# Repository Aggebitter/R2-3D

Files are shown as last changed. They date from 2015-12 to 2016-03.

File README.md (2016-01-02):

# R2-3D

My home brewed coreXY 3d printer
The name "R2-3D" is a tribute to R2-D2 and his creator George Lucas who made me just love things that moves by software, 
electronics and pure mechanics.
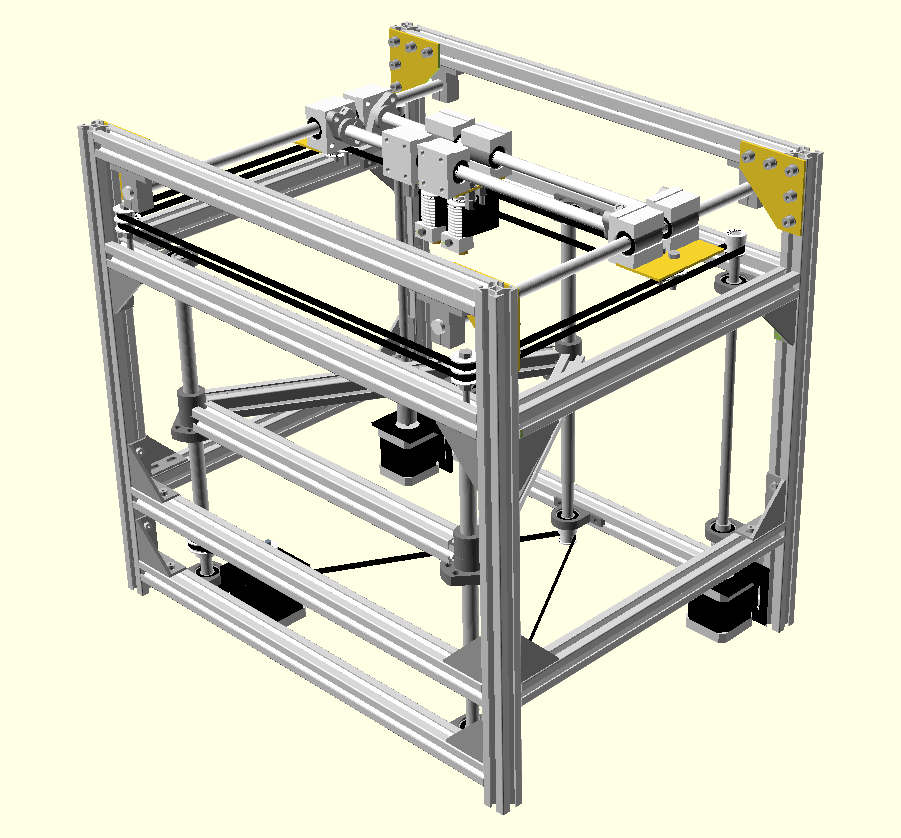
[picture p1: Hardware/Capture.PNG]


History:
A few years ago I put together a 3d printer kit from Welleman. 
It was their K8200 and I call it "put together" because it was like building Lego or Mecchano for us born back in the 70s.
I had a lot of fun with it and the complete build took about 24 hours from opening the box to the first print out.

But after some use I was not so impressed by the prints and a whole summer vacation full of modifications
did not satisfy me. There where too many issues with the design and I soon reached the end of the road.
The mechanics was not an big issue... it was the basic design.

After reading a lot of forum threads,and I meen a lot...! I started to notice a pattern with the same problems occuring in
most of the common and open designs of 3d-printers.

The roundup is as follows:

Z-Axis 
Printbed not as flat as needed for a solid gripping first layer

X and Y differs from the Z plane at diffrent locations due to slack or gravity bend on the axis

Heatbed does not deliver the high temperatures needed for printing ABS and other tough filaments

An asymetric drive of the axis contributes to both a diffrence in the Z-plane and a non perfect angle on the moves

ABS warps due to the fact that it shrinks when getting cold. 

This is all about mechanics!

You can try to fix some in software like autoprobing, primeing the first layer, slack compensate 
and so on, but all is still just quick fixes and if you just change filament you have to start all over and 
re-tweek your firmware

CoreXY:

There are some flavours of this type of coordinate system. But as I see it is only one basic design that is the "real" stuff
ref: http://corexy.com/theory.html

The CoreXY has benifits from other more common coordinate systems. It pulls and holds the movement on the X- and Y-axis in 
four points all the time. It sits on the top of the printer and that makes it possible to have a fixed Z-plane in the X- and 
Y-axis and only a linear move in the verical axis. This is a better aproach from the desings where the printbed moves in more 
than one plane. It gives us higher control of the critical Z-plane and fewer factors that will interfer with the need for high 
precision. 

The design with X- and Y- in the top just invites for a heatchamber. But then we shuold try to minimize the amount of motors and 
electronics in the heated volym. 

This Git is my part on delivering back stuff to the comunity of open source and open designs 
But it is still "in the making" My prototype printer works and it's time to start releasing it

My first dry run https://youtu.be/AdaIRemX2_0

// Agge

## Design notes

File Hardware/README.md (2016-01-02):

The folder OpenSCAD contens files for the R2-3D printer. The files are the base set for the upcomming drawings. 
The set is not complete yet

R2-3D is built on common hardware that you can by from Ebay and your local harware store.
The prototype is made with minimum machining and the design will include both 3D-printable-, CNC-mashining- and handtooling- sketches

The prototype is mecanical solid with 10mm linear bearings and all parts in alumium or steel. 

Micro controller: Arduino Mega

Shield RAMPS 1.4 (reprap.org)

Stepper drivers DRV8825 (more amps and voltage)

Wantai NEMA17 steppers rated 2.5A

Aluminium profiles 20x20mm from http://www.motedis.com or for Swedish users http://www.motedis.se

corner mounts, T-slot nuts and bults from http://www.motedis.com or for Swedish users http://www.motedis.se

Nuts, bolts and brackets mostly from Bauhaus hardware store.

BOM will follow soon

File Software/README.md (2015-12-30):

My Config for the very well written firmware Repteier
ref: http://www.repetier.com/

And my arduino sketch for the supporting Arduino UNO/Nano 
Under  development, not a running code !!!!

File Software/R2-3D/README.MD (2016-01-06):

## R2-3D

This is the very much under developmnet of my supporting co processor for the R2-3D printer.

The concept is to not fidle around in the main printer firmware just sniff the trafic on the serial interface and do some 
other nice taskt like controling RGB leds and making sounds (Well, R2-D2 feels like a good feedback voice for R2-3D9) 
Depending on the final R2-3D it might do the heat chamber controll. 

### main features that are under development is as follows:

Display printer head's and printer bed temperatures (It does sniff att 250000 Kbit and display it on my 7-segment)

RGB leds (noting done yet, just got the hardware)

Sound (noting done yet, just got the hardware, but found some nice files, aka ringtones in MP3 format)
Please Lukas art, Don't kill me for telling ;-)

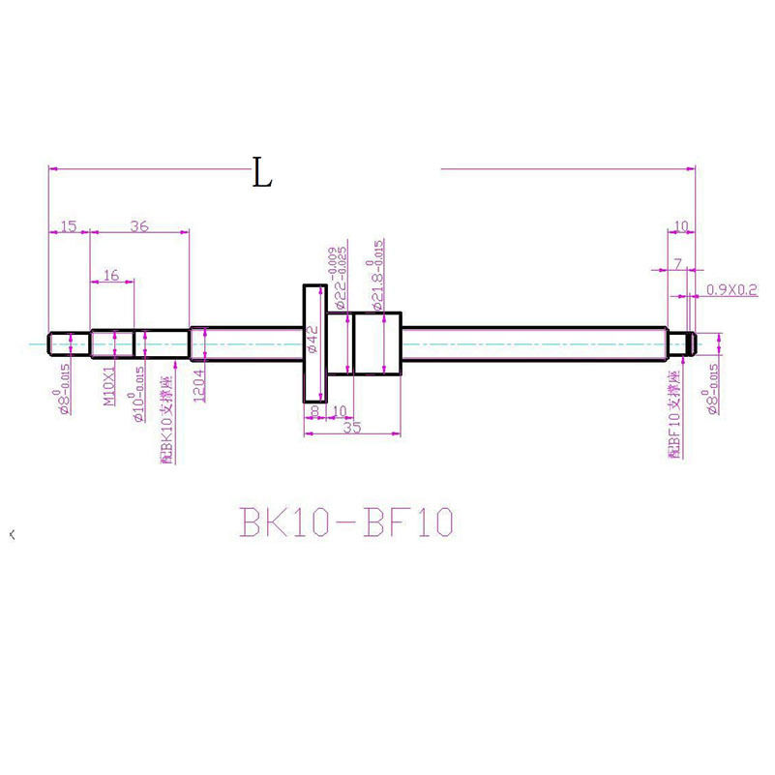
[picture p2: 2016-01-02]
ReferenceDoc/Ballscrew1204_BKBF10.jpg

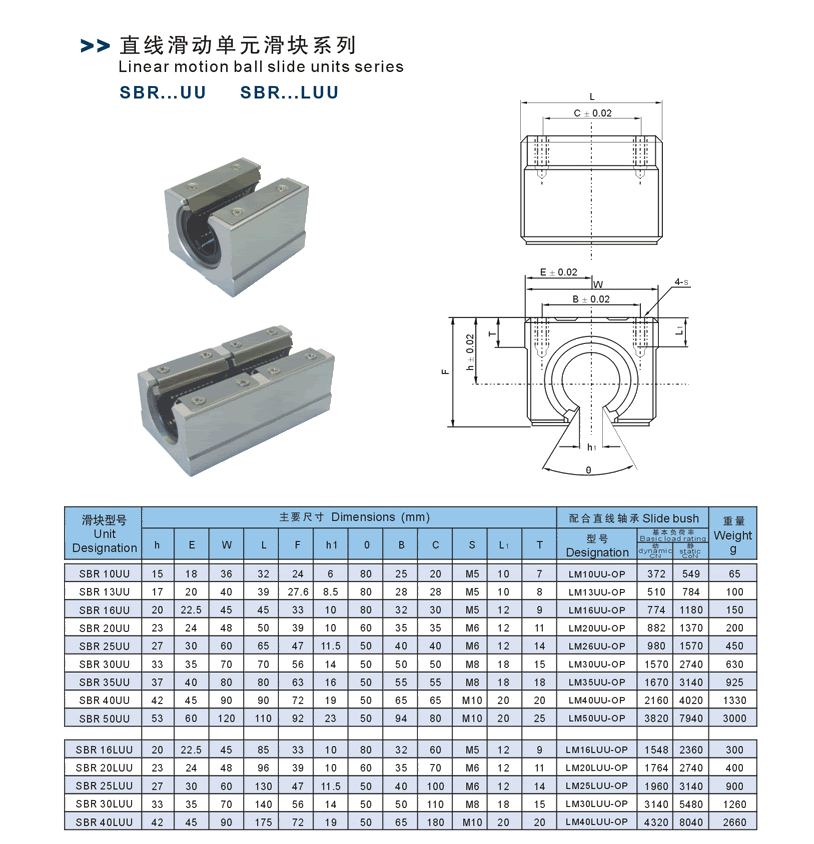
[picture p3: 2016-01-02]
ReferenceDoc/SBRxxUU.gif

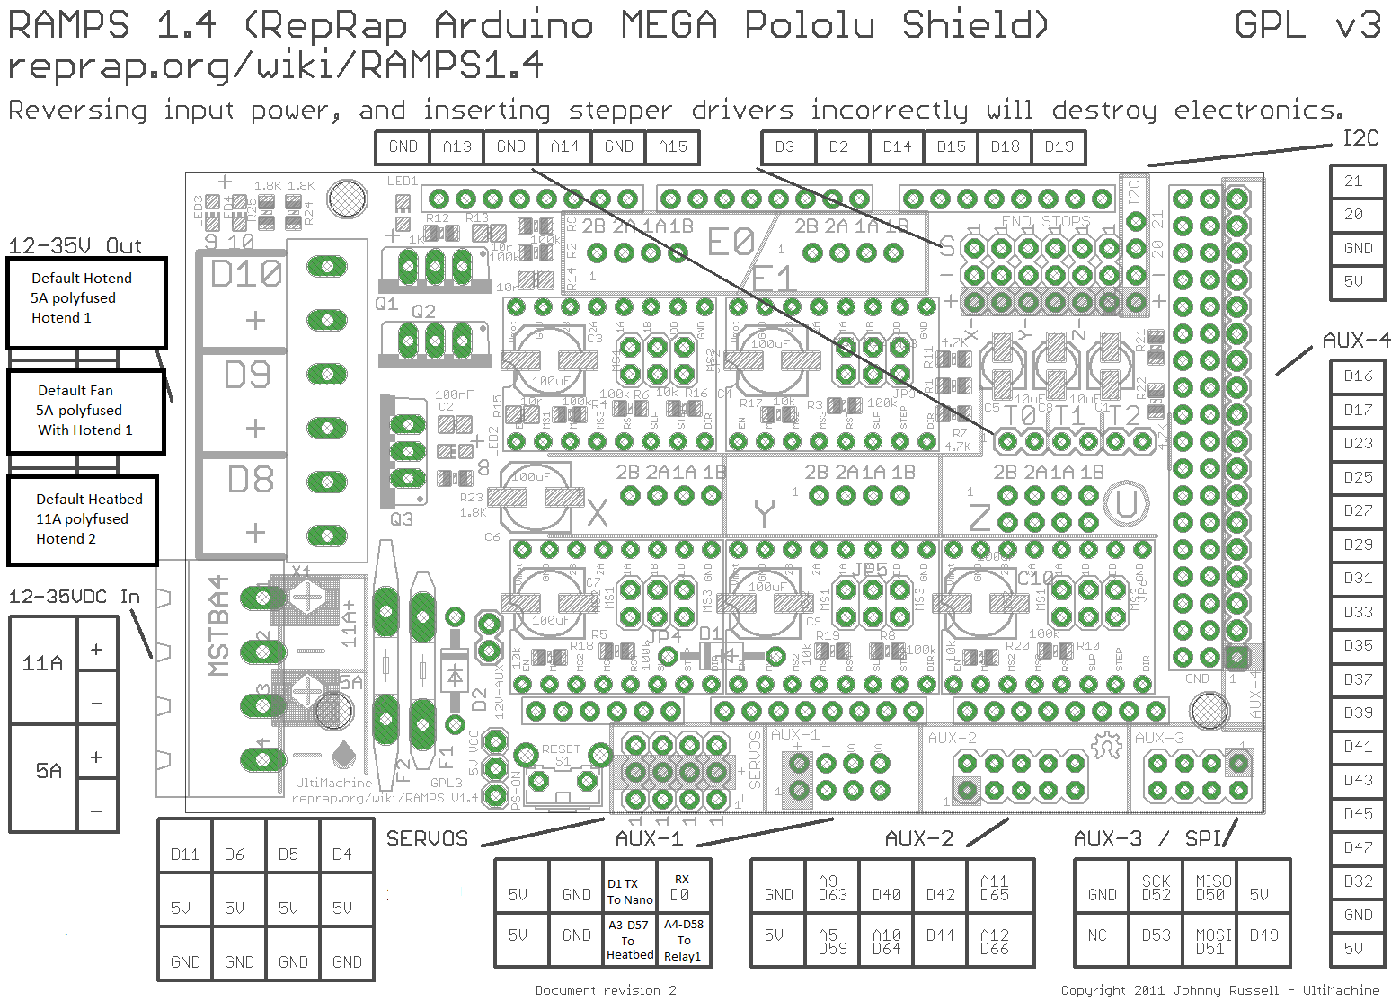
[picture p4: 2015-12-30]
ReferenceDoc/Ramps1.4_R2-3Dv1.0.png

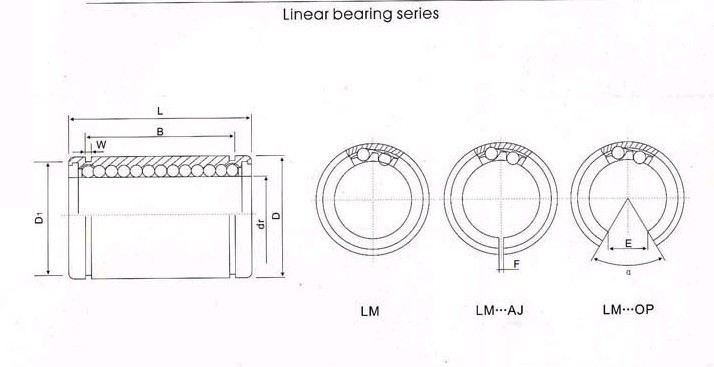
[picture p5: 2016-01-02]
ReferenceDoc/LMxxUU.jpg

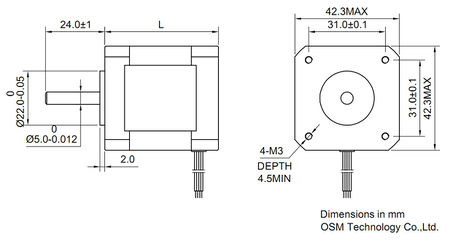
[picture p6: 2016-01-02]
ReferenceDoc/nema_17_stepper_motor.jpg

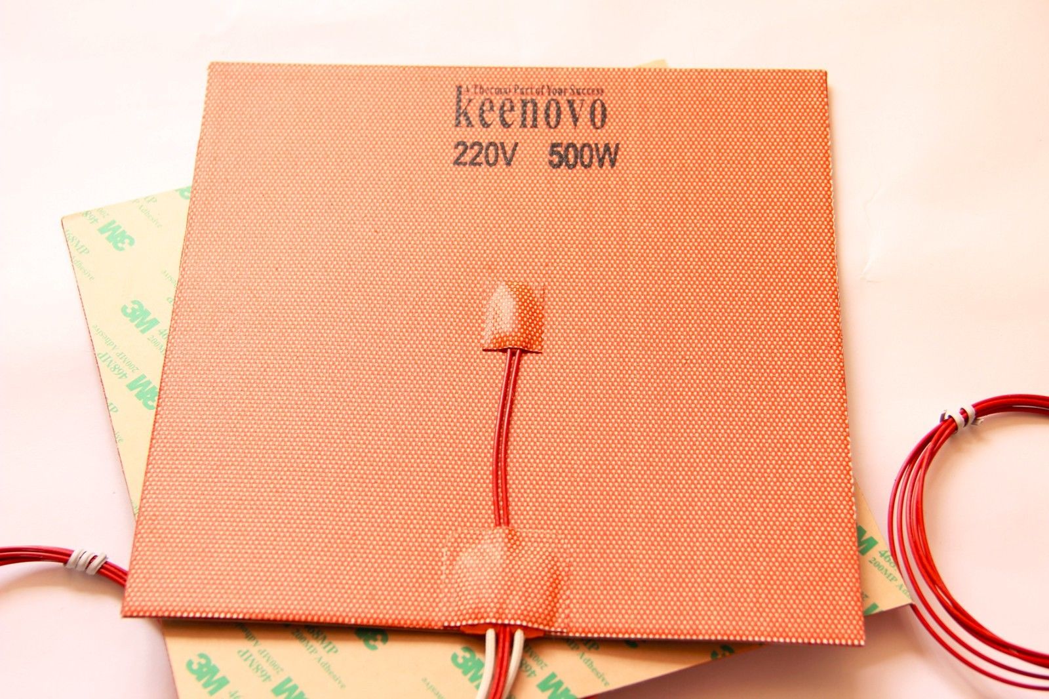
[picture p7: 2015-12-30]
ReferenceDoc/Keenovo.jpg

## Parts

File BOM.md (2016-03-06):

###------------------------  ALUMINIUM PROFILES and mounts -----------------------------

From www.motedis.com (www.motedis.se, for Swedish orders)
 
Profile 20x20 I-Typ slot 5 

Frame
410mm 4pcs (for 300mm ballscrews, if longer ballskrews are used, add the difference in length )
400mm	7pcs
300mm	4pcs

Heatbed mount
290mm	3 pcs

Top
!!!!Not donne yet!!!!!

Bracket 20x40 I-Type slot 5 www.motedis.com (90 degres mount)

18 pcs

T-Nut with spring ball, without guidance I-Type slot 5

200 (two bags) the exact amount not finish yet

Node plate nickel plated aluminum 60x60 (New home made CAD files soon on GitHub)

4 pcs

Aluminium Rod 8mm
300mm 2pcs (for 300mm ballscrews, if longer ballskrews are used, add the difference in length)

###---------------------------------  MECHANICS ----------------------------------------

Ballskrew end maschined 
SFU1204 300mm 3pcs

40 Teeth GT2 Timing Pulley Bore 10mm (drive and gearing down 2:1 Z-axis)
1pcs

20T 5mm GT2 Timing Drive Pulley
1pcs (Z-axis)

20T 8mm GT2 Timing Drive Pulley
5pcs (for CoreXY shafts x2 and ballscrews x3)

Stepper MotorShaft 5x8 mm Flexible Coupling
2 pcs

GT2 timing belt
5m (2.5m for the printer and one spare)

GT2 timing belt loop 
976mm 2pcs (one for spare, Z-axis}

GT2 timing belt loop (this one is to short and i had to machine out some material from the stepper bracket!!)
158mm 2pcs (one for spare, Z-axis}

Axle bearing, self centering 8mm bore
KP08 10pcs

Linear mechanics:
Liner Rail Linear Shaft 10mm diameter
300mm 2pcs
330mm 2pcs

Linear Rod Rail Shaft Support
SHF10 10mm 4pcs

Linear Rail Shaft Guide Support
SK10 10mm 4pcs

Linear Open Bearing 
SBR10UU 10mm 8pcs (Open blocks for matching hole dimensions and max travel, replace the bearings with LM10UU)

Linear Ball Bearing Bush Bushing
LM10UU 10mm 8pcs (for mounting in SBR10UU blocks, see not above)

Alloy Steel Mounting Bracket For 42mm NEMA17 Stepper Motor With Screws 5x5x5cm
5 pcs

Stepper MotorShaft 5x8 mm Flexible Coupling
2 pcs

SG15 5x17x8mm U Groove Sealed Line Track Guide Pulley Rail Ball Bearing (for filament mounting)
6 pcs

#Bolts

Size Lenght amount DIN-standard Standard (Use)

M4 10 10 DIN 7984 (Steel Mounting Bracket For stepper motor [only 8 pcs if only using one extruder)

M4 14 20 DIN 7984 Bore Ball Bearing (KP08)

M4 16 6 DIN 7984 Z-plane

M5 8 93 DIN 7984 (Bracket 20x40 I-Type slot 5 and Optical Endstop Switch)

M5 10 4 DIN 7984 (For Optical Endstop Switch on SBR10UU)

M5 12 8 DIN 7984 Open Linear Bearing, SHF10

M5 14 8 DIN 7984 Linear Rail Shaft Guide (SK10)

M5 16 3 DIN 7984 (For Ball Bearing for Filament)

M5 25 2 x

M5 30 1 y

M5 35 1 Extruderplate

M6 16 8 xy, Open Linear Bearing (SBR10UU)

#T-nut
M4 36 T-slot spring nut, for I-typ T-slot 5mm

M5 116 T-slot spring nut, for I-typ T-slot 5mm

#Spring washer

M4 36

M5 116

###-----------------------------  ELECTRONICS common -----------------------------------

Arduino Mega 2560 
RAMPS v1.4

Nema17 Wantaimotor Stepper  42BYGHW811 4800g.cm 2.5A (For fast print you need amp and voltage)
5pcs

KEENOVO Silicone Heater Pad 20X20cm 500W220V 
HeatedBed 1pcs

5pin 22AWG cable
10m

APTINEX Dual Channel Triac Module MOC3061 BT139 600V 16A (for a 230V 500W AC heatbed on digital pin57)

100K ohm NTC B4267 ATC Semitic 104GT-2 Thermistor
Thermistor 3pcs (You almost never nows what thermistor is used in chines clones, replace them ;-) )

Bowden J-head Hotend E3D V6 extruder
2pcs

MK8 Extruder dedicated Aluminum Frame Block
2pcs

Rocker Switch with red light KCD4-201N 4 pin on/off 16A/250V 
2pcs (Mains and enable/disable heatbed]

Optical Endstop Switch 
RepRap Mendel Prusa modell 3pcs

###--------------------------  ELECTRONICS R2-3D specific  -----------------------------

Supporting processor:
Arduino Nano
Expansion-Board-Terminal-Adapter-DIY-Kits-for-Arduino-NANO-IO-Shield-V1-0-S

5V MAX7219 8-Digit Red LED Display Module 7 Segment (for nice view of current temeratures)
2 pcs 

##Addons ;-)

U-disk audio player TF SD card voice module MP3 Sound WTV020-SD-16P
LM386 Audio Amplifier Module Board 5V-12V (sound is great;)
Loudspeaker 8Ω 0.25W 8ohm Small Trumpet 29mm

Printer head lights:

Adafruit NeoPixel Ring 24 x WS2812 5050 RGB LED (not sure if I am going to use it yet)

WS2801 2801 Dream Color 5050 RGB LED strip
5 meters

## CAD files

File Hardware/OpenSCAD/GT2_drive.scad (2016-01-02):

/*
lib for
20 toothed GT2 belt drive 5mm shaft h =16
20 toothed GT2 belt drive 5mm shaft h =16
40 toothed GT2 belt drive 10mm shaft h =17
*/
module GT2_20_5() { // 20 tothed GT2 belt drive 5mm shaft
$fn=50;
color( "White", 1 ) {
difference (){
    union (){
    cylinder (d = 16, h = 7.5, center = false);
    translate ([0,0,7.5])
    cylinder (d = 12.5, h = 7.5, center = false);
    translate ([0,0,15])
    cylinder (d = 16, h = 1, center = false);
    }
       translate ([0,0,-1])
        cylinder (d = 5, h = 18, center = false); 
}
}
}


module GT2_20_8() { // 20 tothed GT2 belt drive 8mm shaft
$fn=50;
color( "White", 1 ) {
difference (){
    union (){
    cylinder (d = 16, h = 7.5, center = false);
    translate ([0,0,7.5])
    cylinder (d = 12.5, h = 7.5, center = false);
    translate ([0,0,15])
    cylinder (d = 16, h = 1, center = false);
    }
       translate ([0,0,-1])
        cylinder (d = 8, h = 18, center = false); 
}
}

}
module GT2_40_10(){ // 40 tothed GT2 belt drive 10mm shaft
$fn=50;
color( "White", 1 ) {
difference (){
    union (){
    cylinder (d = 18, h = 7, center = false);
    translate ([0,0,7])
    cylinder (d = 29, h = 1, center = false);
    translate ([0,0,8])
    cylinder (d = 25, h = 7, center = false);
    translate ([0,0,15])
    cylinder (d = 29, h = 1, center = false);
    }
       translate ([0,0,-1])
        cylinder (d = 10, h = 18, center = false); 
}
}
}

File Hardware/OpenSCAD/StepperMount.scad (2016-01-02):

/*
Stepper steel mount
NEMA 17 Stepper
*/
$fn=50;
module StepperMount (){     //Stepper steel mount 
color( "Black", 1 ) {
union (){
difference (){
   
     cube ([50,52,53.5]) ; 
    
     // difference starts here  
   translate ([-1,3,3]) 
     cube ([52,52,53.5]) ; 
    hull() {
        translate ([8,3,13]) rotate ([90,0,0])
        cylinder(d=4.2,h=10, center = true);
            translate ([8,3,42]) rotate ([90,0,0])
        cylinder(d=4.2,h=10, center = true);
       }
    hull() {
        translate ([42,3,13]) rotate ([90,0,0])
        cylinder(d=4.2,h=10, center = true);
        translate ([42,3,42]) rotate ([90,0,0])
        cylinder(d=4.2,h=10, center = true);
    }
        translate ([25,31,-1])
        cylinder(d=22,h=10, center = true);
        translate ([10,46,-1])
        cylinder(d=3.5,h=10, center = true);
        translate ([10,15,-1])
        cylinder(d=3.5,h=10, center = true);
        translate ([41,15,-1])
        cylinder(d=3.5,h=10, center = true);
        translate ([41,46,-1])
        cylinder(d=3.5,h=10, center = true);

}
difference (){
        translate ([0,3,3])
        cube ([3,20,15]) ; 
        translate ([4,3,18]) rotate ([127,0,180])
        cube ([5,20,30]) ; 
}
difference (){
        translate ([47,3,3])
        cube ([3,20,15]) ; 
        translate ([51,3,18]) rotate ([127,0,180])
        cube ([5,20,30]) ; 
}
}
}
}
module NEMA17 (){           //NEMA 17 Stepper
translate ([25,31,3.01]) rotate ([0,180,0]) {
$fn=50;
difference (){
union (){
translate ([0,0,-23]){
color( "Black", 1 ) 
difference (){
cube([42,42,30], center = true) ;
      union (){
        difference (){
            rotate ([0,0,45])
            cube([60,60,50], center = true) ;
            rotate ([0,0,45])
            cube([50,50,52], center = true) ;
}}  
    
}

color( "Gainsboro", 1 ) 
difference (){
    union (){
        translate ([0,0,19])
        color( "Gainsboro", 1 ) 
        cube([42,42,8], center = true) ;
        translate ([0,0,-19.5])
        cube([42,42,9], center = true) ;
}
    union (){
        difference (){
            rotate ([0,0,45])
            cube([60,60,50], center = true) ;
            rotate ([0,0,45])
            cube([53.5,53.5,52], center = true) ;
}}}
}

    color( "Gainsboro", 1 ) 
    cylinder (d=22, h=2, center = false);
    color( "LightSlateGray", 1 ) 
    cylinder (d=5, h=24, center = false);
}
translate ([-15.5,-15.5,-10])
cylinder (d=3, h=24, center = false);
translate ([15.5,15.5,-10])
cylinder (d=3, h=24, center = false);
translate ([-15.5,15.5,-10])
cylinder (d=3, h=24, center = false);
translate ([15.5,-15.5,-10])
cylinder (d=3, h=24, center = false);



}


}}


// Place the stepper mounts
    translate ([13,320,56]) rotate ([0,180,180]){
    StepperMount ();
    NEMA17 ();}
    translate ([377,320,56]) rotate ([0,180,180]){
    StepperMount ();
    NEMA17 ();}
    translate ([150,22,53.5]) rotate ([0,180,0]){ 
    // 2mm space for tension adjusting plate
    StepperMount ();
    NEMA17 ();}
    
    
    
    
//  the CoreXY drive shafts and copplers
  color( "Silver", 1 ) {
    translate ([38,289,80]) rotate ([0,0,180])
    cylinder(d=8,h=270, center = false);
    translate ([402,289 ,80]) rotate ([0,0,180])
    cylinder(d=8,h=270, center = false);
        
 color( "Silver", 1 ) {
    translate ([38,289 ,60]) rotate ([0,0,180])
    cylinder(d=18,h=25, center = false);
    translate ([402,289 ,60]) rotate ([0,0,180])
    cylinder(d=18,h=25, center = false);   
}}

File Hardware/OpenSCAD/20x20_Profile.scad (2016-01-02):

/*
20x20 Aluminium T-slot profile from modeus...
*/



 module AluProfile(Lenght){
color( "Gainsboro", 1 ) {
$fn=50;     
    
union () {     
RealLenght = Lenght / 2 ; // bug in OpenScad ?
    difference (){    
        union (){    // the Aluminium base         
           translate ([1,1,0]){ 
               minkowski(){
                cube([18,18,RealLenght]);
                cylinder(r=1,h=RealLenght);
                }}     
        }
// Difference starts here 
   translate ([10,10,0]){   // center hole
       cube([5,5,Lenght*2+1], true);
    }         
        
   union (){                // first T-Slot South
    translate ([10,2,0]){  
       cube([6,8,Lenght*2+1], true);     
    }
   translate ([10,3,0]){  
       cube([8,2,Lenght*2+1], true);      
  }
     translate ([10,2,0]){  
       cube([12.5,1.6,Lenght*2+1], true);      
  }
   translate ([13.9,3.7,0]){ 
       rotate ([0,0,45]) { 
       cube([2,4.5,Lenght*2+1], true);      
  }}
     translate ([6.1,3.7,0]){ 
       rotate ([0,0,45]) { 
       cube([4.5,2,Lenght*2+1], true);      
  }}    
    }  

   translate ([0,20,0]){    // Second T-Slot North
    mirror ([0,1,0]) { 
   union (){                
    translate ([10,2,0]){  
       cube([6,8,Lenght*2+1], true);     
    }
   translate ([10,3,0]){  
       cube([8,2,Lenght*2+1], true);      
  }
     translate ([10,2,0]){  
       cube([12.5,1.6,Lenght*2+1], true);      
  }
   translate ([13.9,3.7,0]){ 
       rotate ([0,0,45]) { 
       cube([2,4.5,Lenght*2+1], true);      
  }}
     translate ([6.1,3.7,0]){ 
       rotate ([0,0,45]) { 
       cube([4.5,2,Lenght*2+1], true);      
  }}    
    }  
}}

translate ([20,0,0]){ // third and forth T-Slot East West
rotate ([0,0,90]) { 
   union (){                
    translate ([10,2,0]){  
       cube([6,8,Lenght*2+1], true);     
    }
   translate ([10,3,0]){  
       cube([8,2,Lenght*2+1], true);      
  }
     translate ([10,2,0]){  
       cube([12.5,1.6,Lenght*2+1], true);      
  }
   translate ([13.9,3.7,0]){ 
       rotate ([0,0,45]) { 
       cube([2,4.5,Lenght*2+1], true);      
  }}
     translate ([6.1,3.7,0]){ 
       rotate ([0,0,45]) { 
       cube([4.5,2,Lenght*2+1], true);      
  }}    
    } 
   translate ([0,20,0]){    
    mirror ([0,1,0]) { 
   union (){                
    translate ([10,2,0]){  
       cube([6,8,Lenght*2+1], true);     
    }
   translate ([10,3,0]){  
       cube([8,2,Lenght*2+1], true);      
  }
     translate ([10,2,0]){  
       cube([12.5,1.6,Lenght*2+1], true);      
  }
   translate ([13.9,3.7,0]){ 
       rotate ([0,0,45]) { 
       cube([2,4.5,Lenght*2+1], true);      
  }}
     translate ([6.1,3.7,0]){ 
       rotate ([0,0,45]) { 
       cube([4.5,2,Lenght*2+1], true);      
  }}    
    }
}}}}   


  } 
}}}



//AluProfile(10);

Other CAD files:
Hardware/OpenSCAD/AluFrame.scad
Hardware/OpenSCAD/BallScrew.scad
Hardware/OpenSCAD/Bearings.scad
Hardware/OpenSCAD/BultsNuts.scad
Hardware/OpenSCAD/CoreXY.scad
Hardware/OpenSCAD/CoreXYv2.0.scad
Hardware/OpenSCAD/CoreXZ.scad
Hardware/OpenSCAD/CornerMount.scad
Hardware/OpenSCAD/GT2Zaxis.scad
Hardware/OpenSCAD/HeatBed.scad
Hardware/OpenSCAD/LShaftMount.scad
Hardware/OpenSCAD/LinearBearing.scad
Hardware/OpenSCAD/MountPlate.scad
Hardware/OpenSCAD/MountPlates.scad
Hardware/OpenSCAD/NEMA17.scad
Hardware/OpenSCAD/PrinterHeads.scad
Hardware/OpenSCAD/R2-3D1.0.scad
Hardware/OpenSCAD/R2-3DAluFrame.scad
Hardware/OpenSCAD/ShaftBearing.scad

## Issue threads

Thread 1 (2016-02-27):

Drill the holes for Axle bearing

Aggebitter, 2016-02-27:
Axle bearing, self centering 8mm bore KP08 has a bit to small mounting holes för a M5 bult. Drill them out.

- [ ]

Aggebitter, 2016-03-06:
Will be added to the wiki assembly instructions later on

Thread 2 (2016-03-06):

Lower Bearing for ball Screw needs mashining

Aggebitter, 2016-03-06:
cut of the bearing to the height of the locking bolts. This is to get enough shaft to mount the 20T 8mm GT2 Timing Drive Pulley

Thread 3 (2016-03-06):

Screws

SweToran, 2016-03-06:
Skruvar
         Längd	Antal
M4	10	        10	     DIN 7984		Stegmotorfäste
M4	14	        20	     DIN 7984		Bore Ball Bearing (KP08)
M4	16	        6	     DIN 7984		Z-planet
M5	8	        92	     DIN 7984		Fästskruv vinkel
M5	12	        8	     DIN 7984		Open Linear Bearing, SHF10
M5	14	        8	     DIN 7984		Linear Rail Shaft Guide (SK10)
M5	25	        2		                 	x
M5	30	        1			                y
M5	35	        1			                Extruderplattan
M6	16	        8			                xy, Open Linear Bearing (SBR10UU)

T-nut
M4		        36			                T-mutter med fjäderboll, för I-typ T-spår 5
M5		        112			                T-mutter med fjäderboll, för I-typ T-spår 5

Fjäderbricka			                        Spring washer
M4		        36
M5		        112

Med dessa skruvar mm behövs det inte borras något i någon profil etc.

Aggebitter, 2016-03-06:
Update BOM with bolts, nuts and spacers..
Will close on final assembly guide

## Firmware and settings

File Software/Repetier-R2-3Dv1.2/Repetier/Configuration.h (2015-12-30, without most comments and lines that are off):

#define CONFIGURATION_H
#define NUM_EXTRUDER 1
#define MOTHERBOARD 33
#include "pins.h"
#undef FAN_BOARD_PIN
#define FAN_BOARD_PIN -1
#define FAN_THERMO_PIN -1
#define FAN_THERMO_MIN_PWM 128
#define FAN_THERMO_MAX_PWM 255
#define FAN_THERMO_MIN_TEMP 45
#define FAN_THERMO_MAX_TEMP 60
#define FAN_THERMO_THERMISTOR_PIN -1
#define FAN_THERMO_THERMISTOR_TYPE 1
#define BLUETOOTH_SERIAL  -1
#define BLUETOOTH_BAUD  115200
#define MIXING_EXTRUDER 0
#define DRIVE_SYSTEM 2
#define XAXIS_STEPS_PER_MM 160
#define YAXIS_STEPS_PER_MM 160
#define ZAXIS_STEPS_PER_MM 1600
#define EXTRUDER_FAN_COOL_TEMP 50
#define PDM_FOR_EXTRUDER 0
#define PDM_FOR_COOLER 0
#define DECOUPLING_TEST_MAX_HOLD_VARIANCE 20
#define DECOUPLING_TEST_MIN_TEMP_RISE 1
#define KILL_IF_SENSOR_DEFECT 0
#define RETRACT_ON_PAUSE 2
#define PAUSE_START_COMMANDS ""
#define PAUSE_END_COMMANDS ""
#define EXT0_X_OFFSET 0
#define EXT0_Y_OFFSET 0
#define EXT0_Z_OFFSET 0
#define EXT0_STEPS_PER_MM 92.59
#define EXT0_TEMPSENSOR_TYPE 97
#define EXT0_TEMPSENSOR_PIN TEMP_0_PIN
#define EXT0_HEATER_PIN HEATER_0_PIN
#define EXT0_STEP_PIN ORIG_E0_STEP_PIN
#define EXT0_DIR_PIN ORIG_E0_DIR_PIN
#define EXT0_INVERSE 0
#define EXT0_ENABLE_PIN ORIG_E0_ENABLE_PIN
#define EXT0_ENABLE_ON 0
#define EXT0_MAX_FEEDRATE 50
#define EXT0_MAX_START_FEEDRATE 20
#define EXT0_MAX_ACCELERATION 5000
#define EXT0_HEAT_MANAGER 1
#define EXT0_WATCHPERIOD 1
#define EXT0_PID_INTEGRAL_DRIVE_MAX 230
#define EXT0_PID_INTEGRAL_DRIVE_MIN 40
#define EXT0_PID_PGAIN_OR_DEAD_TIME 7
#define EXT0_PID_I 2
#define EXT0_PID_D 40
#define EXT0_PID_MAX 255
#define EXT0_ADVANCE_K 0
#define EXT0_ADVANCE_L 0
#define EXT0_ADVANCE_BACKLASH_STEPS 0
#define EXT0_WAIT_RETRACT_TEMP 150
#define EXT0_WAIT_RETRACT_UNITS 0
#define EXT0_SELECT_COMMANDS ""
#define EXT0_DESELECT_COMMANDS ""
#define EXT0_EXTRUDER_COOLER_PIN -1
#define EXT0_EXTRUDER_COOLER_SPEED 255
#define EXT0_DECOUPLE_TEST_PERIOD 12000
#define EXT0_JAM_PIN -1
#define EXT0_JAM_PULLUP 0
#define FEATURE_RETRACTION 1
#define AUTORETRACT_ENABLED 0
#define RETRACTION_LENGTH 3
#define RETRACTION_LONG_LENGTH 13
#define RETRACTION_SPEED 40
#define RETRACTION_Z_LIFT 0
#define RETRACTION_UNDO_EXTRA_LENGTH 0
#define RETRACTION_UNDO_EXTRA_LONG_LENGTH 0
#define RETRACTION_UNDO_SPEED 20
#define FILAMENTCHANGE_X_POS 0
#define FILAMENTCHANGE_Y_POS 0
#define FILAMENTCHANGE_Z_ADD  2
#define FILAMENTCHANGE_REHOME 1
#define FILAMENTCHANGE_SHORTRETRACT 5
#define FILAMENTCHANGE_LONGRETRACT 50
#define JAM_STEPS 220
#define JAM_SLOWDOWN_STEPS 320
#define JAM_SLOWDOWN_TO 70
#define JAM_ERROR_STEPS 500
#define JAM_MIN_STEPS 10
#define JAM_ACTION 1
#define RETRACT_DURING_HEATUP true
#define PID_CONTROL_RANGE 20
#define SKIP_M109_IF_WITHIN 2
#define SCALE_PID_TO_MAX 0
#define TEMP_HYSTERESIS 0
#define EXTRUDE_MAXLENGTH 160
#define NUM_TEMPS_USERTHERMISTOR0 0
#define USER_THERMISTORTABLE0 {}
#define NUM_TEMPS_USERTHERMISTOR1 0
#define USER_THERMISTORTABLE1 {}
#define NUM_TEMPS_USERTHERMISTOR2 0
#define USER_THERMISTORTABLE2 {}
#define USE_GENERIC_THERMISTORTABLE_1
#define GENERIC_THERM1_T0 25
#define GENERIC_THERM1_R0 100000
#define GENERIC_THERM1_BETA 4036
#define GENERIC_THERM1_MIN_TEMP -20
#define GENERIC_THERM1_MAX_TEMP 300
#define GENERIC_THERM1_R1 0
#define GENERIC_THERM1_R2 4700
#define GENERIC_THERM_VREF 5
#define GENERIC_THERM_NUM_ENTRIES 33
#define HEATER_PWM_SPEED 0
#define HAVE_HEATED_BED 1
#define HEATED_BED_MAX_TEMP 200
#define SKIP_M190_IF_WITHIN 3
#define HEATED_BED_SENSOR_TYPE 97
#define HEATED_BED_SENSOR_PIN TEMP_1_PIN
#define HEATED_BED_HEATER_PIN 57
#define HEATED_BED_SET_INTERVAL 5000
#define HEATED_BED_HEAT_MANAGER 2
#define HEATED_BED_PID_INTEGRAL_DRIVE_MAX 255
#define HEATED_BED_PID_INTEGRAL_DRIVE_MIN 80
#define HEATED_BED_PID_PGAIN_OR_DEAD_TIME   196
#define HEATED_BED_PID_IGAIN   33
#define HEATED_BED_PID_DGAIN 290
#define HEATED_BED_PID_MAX 255
#define HEATED_BED_DECOUPLE_TEST_PERIOD 300000
#define MIN_EXTRUDER_TEMP 150
#define MAXTEMP 275
#define MIN_DEFECT_TEMPERATURE 10
#define MAX_DEFECT_TEMPERATURE 290
#define SUPPORT_LASER 0
#define LASER_PIN -1
#define LASER_ON_HIGH 1
#define SUPPORT_CNC 0
#define CNC_WAIT_ON_ENABLE 300
#define CNC_WAIT_ON_DISABLE 0
#define CNC_ENABLE_PIN -1
#define CNC_ENABLE_WITH 1
#define CNC_DIRECTION_PIN -1
#define CNC_DIRECTION_CW 1
#define DEFAULT_PRINTER_MODE 0
#define ENDSTOP_PULLUP_X_MIN false
#define ENDSTOP_X_MIN_INVERTING false
#define MIN_HARDWARE_ENDSTOP_X true
#define ENDSTOP_PULLUP_Y_MIN false
#define ENDSTOP_Y_MIN_INVERTING false
#define MIN_HARDWARE_ENDSTOP_Y true
#define ENDSTOP_PULLUP_Z_MIN false
#define ENDSTOP_Z_MIN_INVERTING false
#define MIN_HARDWARE_ENDSTOP_Z true
#define ENDSTOP_PULLUP_X_MAX false
#define ENDSTOP_X_MAX_INVERTING false
#define MAX_HARDWARE_ENDSTOP_X true
#define ENDSTOP_PULLUP_Y_MAX false
#define ENDSTOP_Y_MAX_INVERTING false
#define MAX_HARDWARE_ENDSTOP_Y true
#define ENDSTOP_PULLUP_Z_MAX false
#define ENDSTOP_Z_MAX_INVERTING false
#define MAX_HARDWARE_ENDSTOP_Z true
#define max_software_endstop_r true
#define min_software_endstop_x false
#define min_software_endstop_y false
#define min_software_endstop_z false
#define max_software_endstop_x false
#define max_software_endstop_y false
#define max_software_endstop_z false
#define ENDSTOP_X_BACK_MOVE 5
#define ENDSTOP_Y_BACK_MOVE 5
#define ENDSTOP_Z_BACK_MOVE 2
#define ENDSTOP_X_RETEST_REDUCTION_FACTOR 3
#define ENDSTOP_Y_RETEST_REDUCTION_FACTOR 3
#define ENDSTOP_Z_RETEST_REDUCTION_FACTOR 3
#define ENDSTOP_X_BACK_ON_HOME 1
#define ENDSTOP_Y_BACK_ON_HOME 1
#define ENDSTOP_Z_BACK_ON_HOME 0
#define ALWAYS_CHECK_ENDSTOPS 1
#define X_ENABLE_ON 0
#define Y_ENABLE_ON 0
#define Z_ENABLE_ON 0
#define DISABLE_X 0
#define DISABLE_Y 0
#define DISABLE_Z 0
#define DISABLE_E 0
#define INVERT_X_DIR 0
#define INVERT_Y_DIR 0
#define INVERT_Z_DIR 0
#define X_HOME_DIR -1
#define Y_HOME_DIR -1
#define Z_HOME_DIR -1
#define X_MAX_LENGTH 180
#define Y_MAX_LENGTH 180
#define Z_MAX_LENGTH 120
#define X_MIN_POS 0
#define Y_MIN_POS 0
#define Z_MIN_POS 0
#define DISTORTION_CORRECTION 0
#define DISTORTION_CORRECTION_POINTS 5
#define DISTORTION_CORRECTION_R 100
#define DISTORTION_PERMANENT 1
#define DISTORTION_UPDATE_FREQUENCY 15
#define DISTORTION_START_DEGRADE 0.5
#define DISTORTION_END_HEIGHT 1
#define DISTORTION_EXTRAPOLATE_CORNERS 0
#define FEATURE_BABYSTEPPING 1
#define BABYSTEP_MULTIPLICATOR 1
#define DELTA_SEGMENTS_PER_SECOND_PRINT 180 // Move accurate setting for print moves
#define DELTA_SEGMENTS_PER_SECOND_MOVE 70 // Less accurate setting for other moves
#define EXACT_DELTA_MOVES 1
#define DELTA_HOME_ON_POWER 0
#define DELTASEGMENTS_PER_PRINTLINE 24
#define STEPPER_INACTIVE_TIME 360L
#define MAX_INACTIVE_TIME 0L
#define MAX_FEEDRATE_X 200
#define MAX_FEEDRATE_Y 200
#define MAX_FEEDRATE_Z 20
#define HOMING_FEEDRATE_X 40
#define HOMING_FEEDRATE_Y 40
#define HOMING_FEEDRATE_Z 20
#define HOMING_ORDER HOME_ORDER_YXZ
#define ZHOME_MIN_TEMPERATURE 0
#define ZHOME_HEAT_ALL 1
#define ZHOME_HEAT_HEIGHT 20
#define ZHOME_X_POS 999999
#define ZHOME_Y_POS 999999
#define ENABLE_BACKLASH_COMPENSATION 0
#define X_BACKLASH 0
#define Y_BACKLASH 0
#define Z_BACKLASH 0
#define RAMP_ACCELERATION 1
#define STEPPER_HIGH_DELAY 0
#define DIRECTION_DELAY 0
#define STEP_DOUBLER_FREQUENCY 12000
#define ALLOW_QUADSTEPPING 1
#define DOUBLE_STEP_DELAY 0 // time in microseconds
#define MAX_ACCELERATION_UNITS_PER_SQ_SECOND_X 1000
#define MAX_ACCELERATION_UNITS_PER_SQ_SECOND_Y 1000
#define MAX_ACCELERATION_UNITS_PER_SQ_SECOND_Z 100
#define MAX_TRAVEL_ACCELERATION_UNITS_PER_SQ_SECOND_X 1000
#define MAX_TRAVEL_ACCELERATION_UNITS_PER_SQ_SECOND_Y 1000
#define MAX_TRAVEL_ACCELERATION_UNITS_PER_SQ_SECOND_Z 100
#define INTERPOLATE_ACCELERATION_WITH_Z 0
#define ACCELERATION_FACTOR_TOP 100
#define MAX_JERK 10
#define MAX_ZJERK 0.3
#define PRINTLINE_CACHE_SIZE 16
#define MOVE_CACHE_LOW 10
#define LOW_TICKS_PER_MOVE 250000
#define FEATURE_TWO_XSTEPPER 0
#define X2_STEP_PIN   ORIG_E1_STEP_PIN
#define X2_DIR_PIN    ORIG_E1_DIR_PIN
#define X2_ENABLE_PIN ORIG_E1_ENABLE_PIN
#define FEATURE_TWO_YSTEPPER 0
#define Y2_STEP_PIN   ORIG_E1_STEP_PIN
#define Y2_DIR_PIN    ORIG_E1_DIR_PIN
#define Y2_ENABLE_PIN ORIG_E1_ENABLE_PIN
#define FEATURE_TWO_ZSTEPPER 0
#define Z2_STEP_PIN   ORIG_E1_STEP_PIN
#define Z2_DIR_PIN    ORIG_E1_DIR_PIN
#define Z2_ENABLE_PIN ORIG_E1_ENABLE_PIN
#define FEATURE_THREE_ZSTEPPER 0
#define Z3_STEP_PIN   ORIG_E2_STEP_PIN
#define Z3_DIR_PIN    ORIG_E2_DIR_PIN
#define Z3_ENABLE_PIN ORIG_E2_ENABLE_PIN
#define FEATURE_DITTO_PRINTING 0
#define USE_ADVANCE 0
#define ENABLE_QUADRATIC_ADVANCE 0
#define BAUDRATE 250000
#define ENABLE_POWER_ON_STARTUP 1
#define POWER_INVERTING 0
#define KILL_METHOD 1
#define ACK_WITH_LINENUMBER 1
#define WAITING_IDENTIFIER "wait"
#define ECHO_ON_EXECUTE 1
#define EEPROM_MODE 1
#undef PS_ON_PIN
#define PS_ON_PIN ORIG_PS_ON_PIN
#define JSON_OUTPUT 0
#define FEATURE_SERVO 0
#define SERVO0_PIN 11
#define SERVO1_PIN -1
#define SERVO2_PIN -1
#define SERVO3_PIN -1
#define SERVO0_NEUTRAL_POS  -1
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

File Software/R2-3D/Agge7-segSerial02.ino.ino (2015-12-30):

#include "LedControl.h"
/*
 Now we need a LedControl to work with.
 ***** These pin numbers will probably not work with your hardware *****
 pin 12 is connected to the DataIn 
 pin 11 is connected to the CLK 
 pin 10 is connected to LOAD 
 We have only a single MAX72XX.
 */
LedControl lc=LedControl(12,11,10,1);
/* we always wait a bit between updates of the display */
unsigned long delaytime=250;





/*
Example of processing incoming serial data without blocking.

Author:   Nick Gammon
Date:     13 November 2011. 
Modified: 31 August 2013.

Released for public use.
*/

// how much serial data we expect before a newline
const unsigned int MAX_INPUT = 50;
String matchingString = "T:";    // match the first two letters in M105 response
String inputString = ""; 
void setup ()
  {
  Serial.begin (250000);
  /*
   The MAX72XX is in power-saving mode on startup,
   we have to do a wakeup call
   */
  lc.shutdown(0,false);
  /* Set the brightness to a medium values */
  lc.setIntensity(0,1);
  /* and clear the display */
  lc.clearDisplay(0);
  writeAggeOn7Segment();
  } // end of setup


/*
 This method will display the characters for the
   word "Arduino" rolling on 8pc 7segment
   */
  void writeAggeOn7Segment() {
   lc.clearDisplay(0);
  for(int i=-8;i<8;i++) {
  lc.setChar(0,i,' ',false);      // Space
  lc.setChar(0,i+1,' ',false);    // Space
  lc.setChar(0,i+2,' ',false);    // Space
  lc.setChar(0,i+3,' ',false);    // Space
  lc.setChar(0,i+4,'E',false);    // E
  lc.setChar(0,i+5,'6',false);    // G
  lc.setChar(0,i+6,'6',false);    // G
  lc.setChar(0,i+7,'a',false);    // A

  delay(delaytime);
 lc.setChar(0,4,'1',false);
  }
} 


// here to process incoming serial data after a terminator received
// void process_data (const char * data)
void process_data (const String data)
  {
  // for now just display it
  // (but you could compare it to some value, convert to an integer, etc.)
   
String currentTemp0;
String targetTemp0;
String currentTemp1;
String targetTemp1;
String current7Seg0;
float cTemp0;
float tTemp0;

int indexCurrent0;
int indexCurrent1;
int indexCurrent2;
int indexCurrent3;
  //inputString = data;
  if (data.substring(0, 2) == matchingString) {
    // format is T:18.76 /0 B:17.78 /0 B@:0 @:0   
    // get the indexes för the 8 temperatures
    indexCurrent0 = data.indexOf(' ');
    indexCurrent1 = data.indexOf(' ',indexCurrent0 + 1);
    indexCurrent2 = data.indexOf(' ',indexCurrent1 + 1);
    indexCurrent3 = data.indexOf(' ',indexCurrent2 + 1);
    
    currentTemp0 =  data.substring(2, indexCurrent0);
    targetTemp0 =  data.substring(indexCurrent0 +2 , indexCurrent1);


    currentTemp1 =  data.substring(indexCurrent1 + 3, indexCurrent2);
    targetTemp1 =  data.substring(indexCurrent2 +2 , indexCurrent3);

      
       current7Seg0 = currentTemp0.substring(4, 5);
       lc.setChar(0,4,(current7Seg0.toInt()),false);
         current7Seg0 = currentTemp0.substring(3, 4);
         lc.setChar(0,5,(current7Seg0.toInt()),false);
           current7Seg0 = currentTemp0.substring(1, 2);
           lc.setChar(0,6,(current7Seg0.toInt()),false);
             current7Seg0 = currentTemp0.substring(0, 1);
             lc.setChar(0,7,(current7Seg0.toInt()),false);
             
    // convert to float
    cTemp0 = currentTemp0.toFloat();
    cTemp0 = cTemp0 * 100 ;
    tTemp0 = targetTemp0.toFloat(); 
             
        Serial.println(cTemp0);
  }
else {
   Serial.println (data);
}
  }  // end of process_data
  
void processIncomingByte (const byte inByte)
  {
  static char input_line [MAX_INPUT];
  static unsigned int input_pos = 0;

  switch (inByte)
    {

    case '\n':   // end of text
      input_line [input_pos] = 0;  // terminating null byte
      
      // terminator reached! process input_line here ...
      process_data (input_line);
      
      // reset buffer for next time
      input_pos = 0; 

      break;

    case '\r':   // discard carriage return
      break;

    default:
      // keep adding if not full ... allow for terminating null byte
      if (input_pos < (MAX_INPUT - 1))
        input_line [input_pos++] = inByte;
      break;

    }  // end of switch
   
  } // end of processIncomingByte  

void loop()
  {
  // if serial data available, process it
  while (Serial.available () > 0)
    processIncomingByte (Serial.read ());
    
  // do other stuff here like testing digital input (button presses) ...

  }  // end of loop

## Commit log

2015-12-30 Create R2-3D.scad
    the main compile file, just includes everything
    [R2-3D.scad]
2015-12-30 Just clean up
    [20x20_Profile.scad, AluFrame.scad, Configuration.h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]
2015-12-30 more cleaning
    [20x20_Profile.scad, AluFrame.scad, CornerMount.scad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]
2016-01-02 Major update on the printer hardware almost complete
    Heat bed not finished yet
    [20x20_Profile.scad, AluFrame.scad, BallScrew.scad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]
2016-01-02 New fast rendering
    Heat bed is not complete
2016-01-05 Create BOM.TXT
    Not complete yet
    Profiles from www.motedis.com (www.motedis.se, for Swedish orders)
    Aluminium profiles is almost complete. Missing the lid for chamber build (not constructed yet
2016-01-06 Update BOM.TXT
    I'm sure that I have missed something
2016-01-06 Update BOM.md
    Still missing some parts
2016-03-06 Update BOM.md
    Updated some of the list for the bolts, nuts and washers.

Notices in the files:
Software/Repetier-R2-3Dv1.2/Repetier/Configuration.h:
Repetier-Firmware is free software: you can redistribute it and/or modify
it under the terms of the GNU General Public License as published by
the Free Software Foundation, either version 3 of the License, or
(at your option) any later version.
